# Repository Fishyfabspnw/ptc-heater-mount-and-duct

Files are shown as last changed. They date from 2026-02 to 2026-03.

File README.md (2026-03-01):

# PTC Heater Mount and Duct




## Installation Instructions

### ⚠️ Safety Notice
This mount is intended for use with PTC heaters inside enclosed 3D printers.
Ensure all wiring is properly insulated and strain-relieved. (Ensure a thermal cutoff fuse is implemented directly touching the heater)
Never power the heater without proper thermal control and safety protection.

---

### Required Hardware

-BOM (https://github.com/Fishyfabspnw/ptc-heater-mount-and-duct/blob/main/BOM.md#bill-of-materials)
- High-temp wire (silicone insulated recommended/ or FEP wire)
- Thermal fuse (REQUIRED!!!)
- SSR( Solid State Relay)
- Cartridge Style Thermistor

---

### Print Recommendations For Wire Shroud (High Temp FILAMENTS ONLY!!!)

Material: ASA-GF / PPS-CF / NYLON 
Do NOT use PLA inside heated chambers.  
Walls: 4+  
Infill: 45%+  
First Layer Height: 0.25mm
Layer Height: 0.2mm    
Seam: Back

---

### Assembly Steps

1. Prep SLM/Laser Cut part by tapping.  
2. Implement a 121c thermal cutoff fuse to the power loop. Safely drill a hole through the fins in the PTC-Heater to allow for a thermistor to be placed into the fins, apply boron nitrade paste into the hole and then insert the thermistor. (i drilled and used a rivet, and ring terminal around the rivot then attatched the 121c thermal cutoff fuse to that and bent it so it was making contact with the heater, apply Red RTV sealant here if needed.). 

4. Apply Boron Nitrade paste into the hole before embedding the thermistor. 
5. Mount standoff's on the orginal PTC Heater shroud with the M4x8mm SHCS.

6. Mount the SLM printed duct to the other side of the standoff with the M4x8mm SHCS.

7. Mount fan and laser cut Part. (The laser cut part is meant to be sandwiched between the fan and the SLM printed duct)

8. Mount wire shroud over the front with the M3x45mm SHCS.

9. Mount the assembly to the extrusion with the M5x8mm SHCS.

---

### Recommended Operating Limits

- Max chamber temperature: [85c]
- Heater wattage tested: [250W]
- Max Heater Temp [110c]

---

### Notes

- Designed for enclosed CoreXY-style printers.
- Ensure adequate airflow across heater fins.
- Add a thermal fuse in series for additional safety.

## Contents

* `Cad` – STEP CAD exports.
*  `SLM` – SLM Parts.
*  `Laser Cut Part` – Sheet Metal Parts.
* `BOM.md` – bill of materials with suppliers/part numbers.

## Heater

This mount and duct is designed for the [PTC Heater](https://www.amazon.com/dp/B07NYX5DKD).

## License

This project is licensed under the [Creative Commons Attribution 4.0 International](https://creativecommons.org/licenses/by/4.0/) (CC BY 4.0) license. See the `LICENSE` file for details.

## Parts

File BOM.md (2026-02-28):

# Bill of Materials

## Heater
This assembly is designed for the **PTC Heater** Listed Below!!

## Parts
| Item | Description | Quantity | Supplier / Part # |
|---|---|---|---|
| 1 | 110V PTC HEATER <br>  | 1 |  – https://www.amazon.com/dp/B07NYX5DKD |
| 2 | 19 mm Stainless Steel Standoff <br>  | 2 | McMaster‑Carr 94868A043 – https://www.mcmaster.com/94868A043/ |
| 3 | Hexagon Socket Head Cap Screw - M5 x 0.8 x 8 Steel 4.6 Plain <br>  | 2 | McMaster‑Carr 91292A191 – https://www.mcmaster.com/91292A191/ |
| 4 | Hexagon Socket Head Cap Screw - M4 x 0.7 x 40 Steel 4.6 Plain <br>  | 4 | McMaster‑Carr 91502A133 –https://www.mcmaster.com/91502A133/ |
| 5 | Hexagon Socket Head Cap Screw - M3 x 0.5 x 8 Steel 4.6 Plain <br>  | 4 | McMaster‑Carr 90751A111 –https://www.mcmaster.com/90751A111/ |
| 6 | Hexagon Socket Head Cap Screw - M3 x 0.5 x 45 Steel 4.6 Plain <br> | 2 | McMaster‑Carr 91292A025 –https://www.mcmaster.com/91292A025/ |
| 7 | Hexagon Socket Head Cap Screw - M4 x 0.7 x 8 Steel 4.6 Plain <br>  | 4 | McMaster‑Carr 90751A115 –https://www.mcmaster.com/90751A115/ |

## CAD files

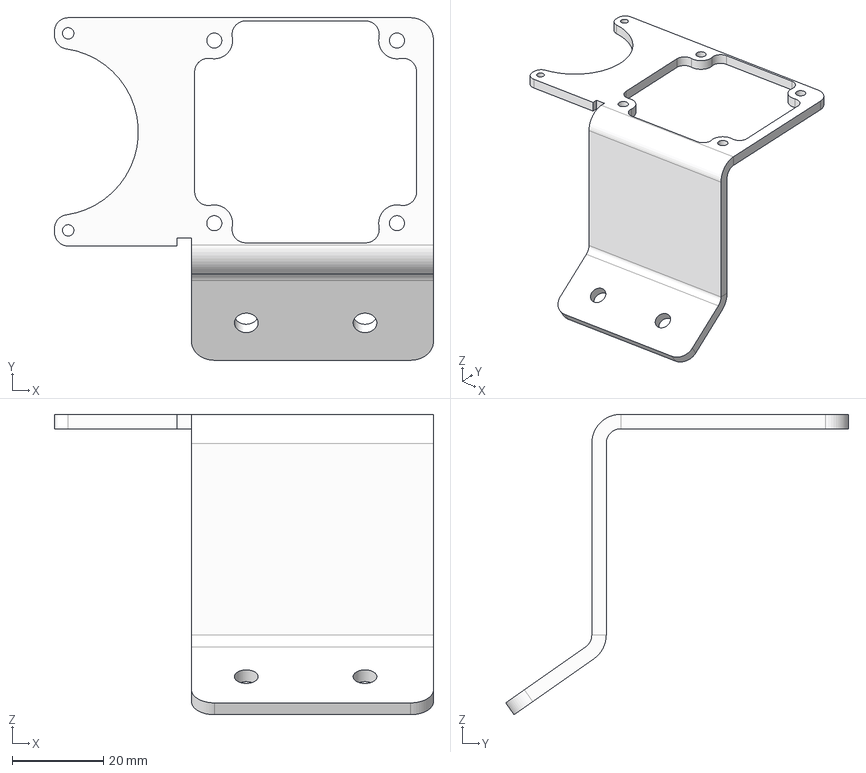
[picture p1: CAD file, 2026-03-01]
Laser Cut Part/BRACKET_LASER_CUT.step
83.0 x 75.0 x 65.8 mm

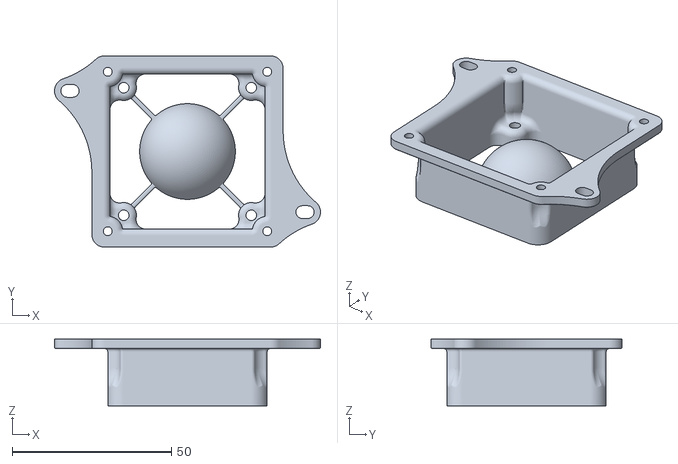
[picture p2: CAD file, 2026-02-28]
SLM/SLM_PRINTED_DUCT.stl
83.4 x 60.0 x 21.0

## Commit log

2026-02-28 Add heater link to README and BOM
2026-02-28 Reformat BOM with separate Heater section
2026-02-28 Refer to heater simply as PTC Heater
2026-02-28 Switch to CC BY 4.0 license
2026-02-28 Add 6mm spacers to BOM
2026-02-28 Correct standoff description and add link
2026-02-28 Include McMaster URL in BOM row
2026-02-28 Embed standoff image placeholder in BOM
2026-02-28 Add standoff image
2026-02-28 Move standoff image to models/PNG and update BOM link
2026-02-28 Create PTC HEATER MOUNT.STEP
2026-03-01 Create Laser Cut Part.step
    [Laser Cut Part.step]
